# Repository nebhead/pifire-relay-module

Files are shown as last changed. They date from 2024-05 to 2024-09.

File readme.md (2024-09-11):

# PiFire Mechanical Relay Module PCB (v1.0.2) KiCad Files

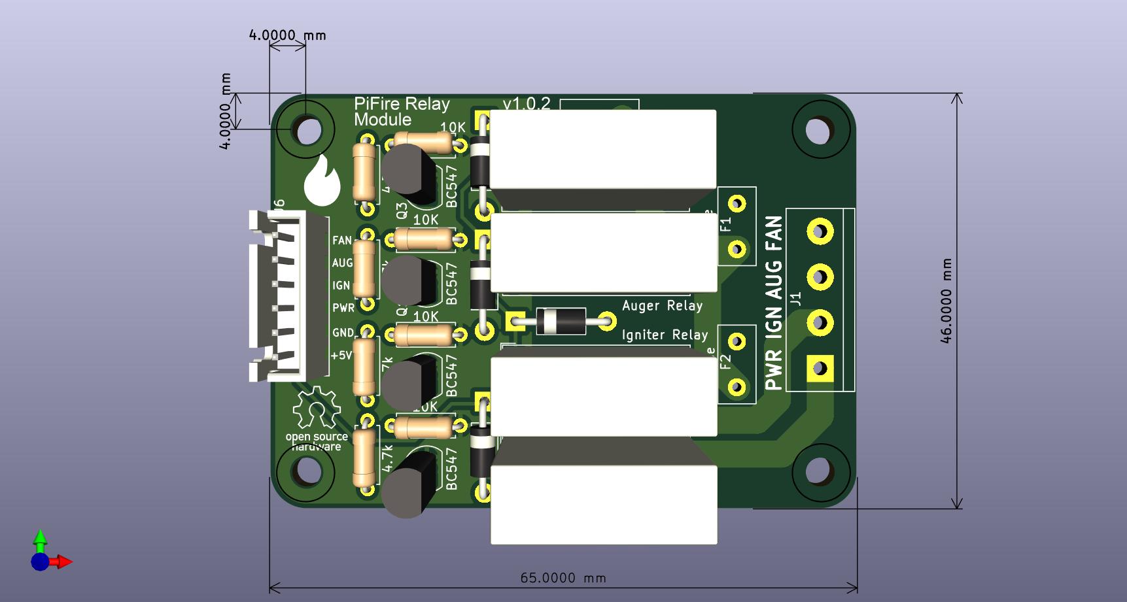
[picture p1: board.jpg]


## What is this? 

This PCB is designed to support mechanical relays for controlling incoming Power(L) to the Igniter, Auger, and AC Fan.  This board uses compact mechanical relays that are able to handle high power. This is an alternative to using an off the shelf relay module which simplifies the wiring and even allows you to use the OEM harness.  

The design intent for this board was to make a DIY accessible PCB that can be more easily put together by the maker/enthusiast of almost any skill level.  Full size components are used in most cases and most (if not all) parts should be readily available to order online.  See the [Interactive BOM](#interactive-bom) for more details about the parts used and links to order.

### What is PiFire? 

PiFire is a SBC based Pellet Smoker Controller.  More details can be found [here](https://nebhead.github.io/PiFire) or [at the GitHub repo](https://github.com/nebhead/pifire). 

## What's in this Repository?

### KiCad Project Files 
In this repository you will find the latest KiCad design files for the  PCB.  Simply load the project file (.kicad_pro) into the KiCad software and you should be able to edit as needed.  Or if you just want to get this board made, jump to the production section below.

### Interactive BOM

There is an interactive BOM located in the [/bom](bom/) folder which details the parts and provides some pin information as well.  Use this to gather the components you may need to build this board out and refer back to it for placement help.    

[BOM + Pin Info](https://nebhead.github.io/pifire-relay-module)

_This is a standalone HTML file that was autogenerated by the excellent plugin for KiCad. See the plugin here: [https://github.com/openscopeproject/InteractiveHtmlBom](https://github.com/openscopeproject/InteractiveHtmlBom)_

### PDF of the Schematic

Preview the schematic in PDF format here: [Schematic](schematic.pdf)

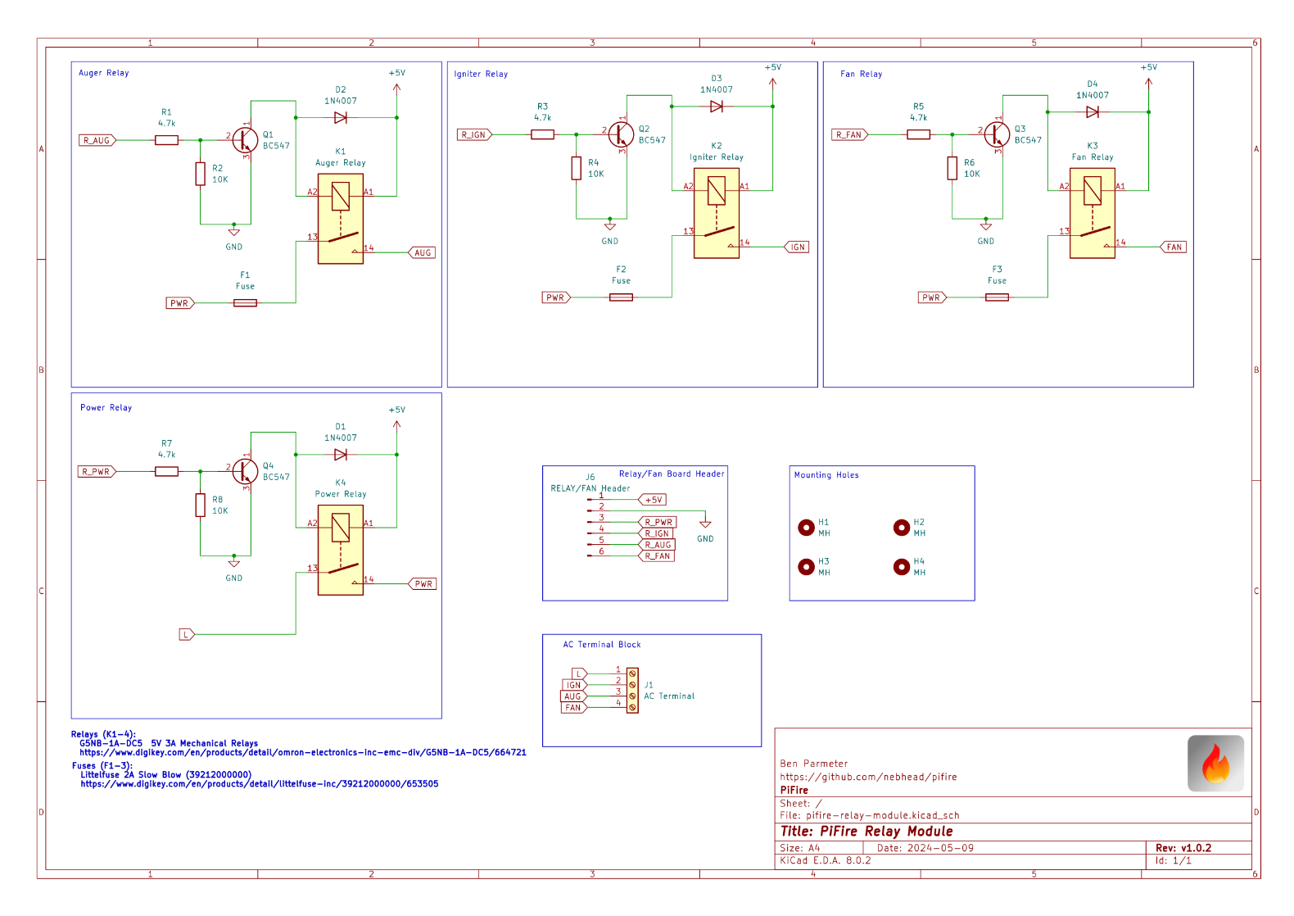
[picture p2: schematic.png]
Schematic PNG


### JLCPCB Production Files

If you wish to get these PCBs made by JLCPCB, the production files are provided in the `/production` folder.  For convenience, the file `production.zip` can simply be uploaded to JLCPCB to make it super easy to order boards.

Drop the zip file onto the order page, wait for it to upload then simply continue to order the board.  Optionally, select different board color, PCB quantity, surface finish, etc.  Most of the default settings should be sufficient. 

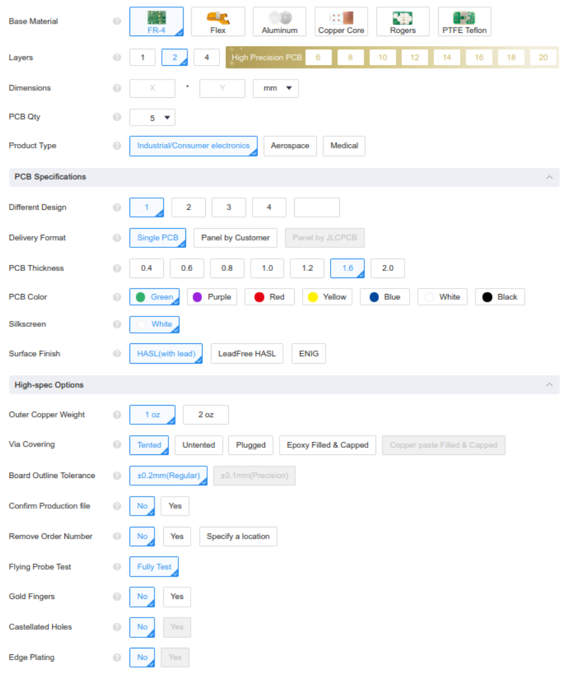
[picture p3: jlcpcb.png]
JLCPCB Order Page


### Links to the PCBs in this family of PiFire Boards

This PCB is part of a family of PCBs that can be used together to create  a full PiFire system.  Generally speaking you need the Main Module/Board, a Relay Control Board and a Probe Device board to have a basic PiFire system.  

**Main Module/Board** (required)
* [Main Board v4.0.x](https://github.com/nebhead/pifire-main-module-nopwr)

**Relay/Fan Control Boards** (choose one)
* [Mechanical Relay Module](https://github.com/nebhead/pifire-relay-module)
* [Solid State Relay Module](https://github.com/nebhead/pifire-relay-module-SSR)
* [Solid State Relay + PWM Fan Module](https://github.com/nebhead/pifire-relay-pwm-module-ssr) - Original Design
* [Solid State Relay + PWM Fan Module Alternate](https://github.com/nebhead/pifire-relay-pwm-module-ssr-alt) - Updated Design (Designed with help from @labmonkeyrat on Discord)

**Probe Device Board** (optional)
* [ADS Board](https://github.com/nebhead/pifire-ads-board) 

### 3D Printable Enclosures/Boxes 

With all of the 3D Prints for PiFire, a higher temperature filament such as PETG should be used.  PLA generally won't stand up to the temperatures that the components may be exposed to outdoors and near a hot smoker.  

#### Enclosure

Included here is an initial revision of the enclosure for this PCB.  The current models should be considered still in development and may have alignment challenges, etc. 

Except for the mounting wings, the majority of bolts to be used with this enclosure are M3. 

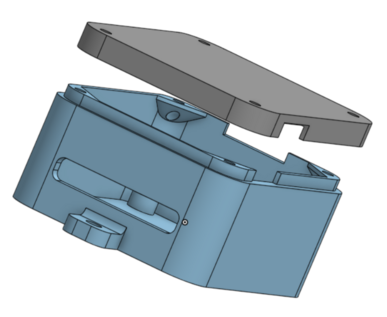
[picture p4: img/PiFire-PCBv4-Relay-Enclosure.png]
Enclosure


* STL: [Base](/printables/PiFire-v4-Relay-Base.stl)
* STL: [Lid](/printables/PiFire-v4-Relay-Lid.stl)
* OnShape: [Enclosure Original Models](https://cad.onshape.com/documents/03559f76f7adf190bf6f1259/w/7529cb0e4cd69db1a6a15202/e/07d5f9d46dc8f2b9e7dd655f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)

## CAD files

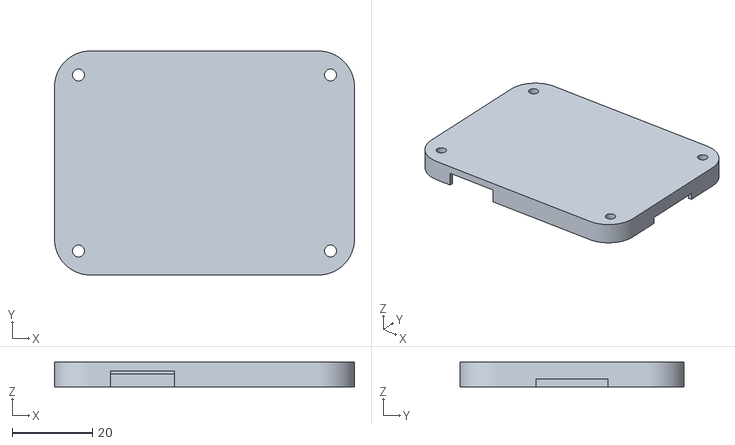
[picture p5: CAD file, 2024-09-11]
printables/PiFire-v4-Relay-Lid.stl
75.0 x 56.0 x 6.20

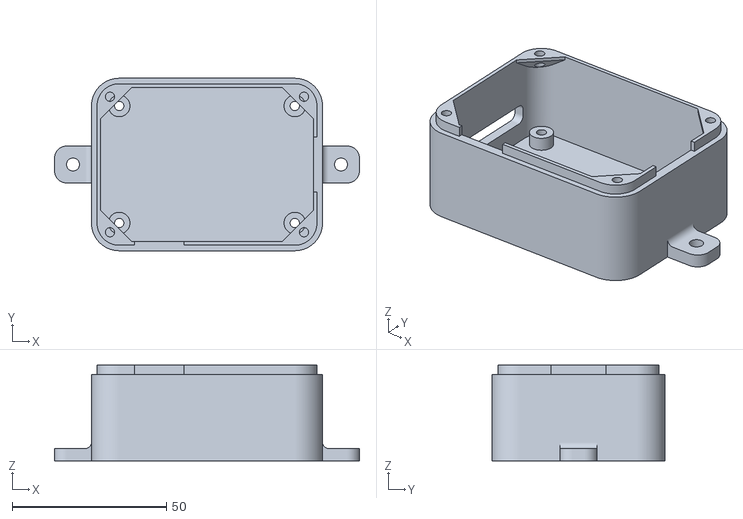
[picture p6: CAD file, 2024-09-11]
printables/PiFire-v4-Relay-Base.stl
99.0 x 56.0 x 31.0

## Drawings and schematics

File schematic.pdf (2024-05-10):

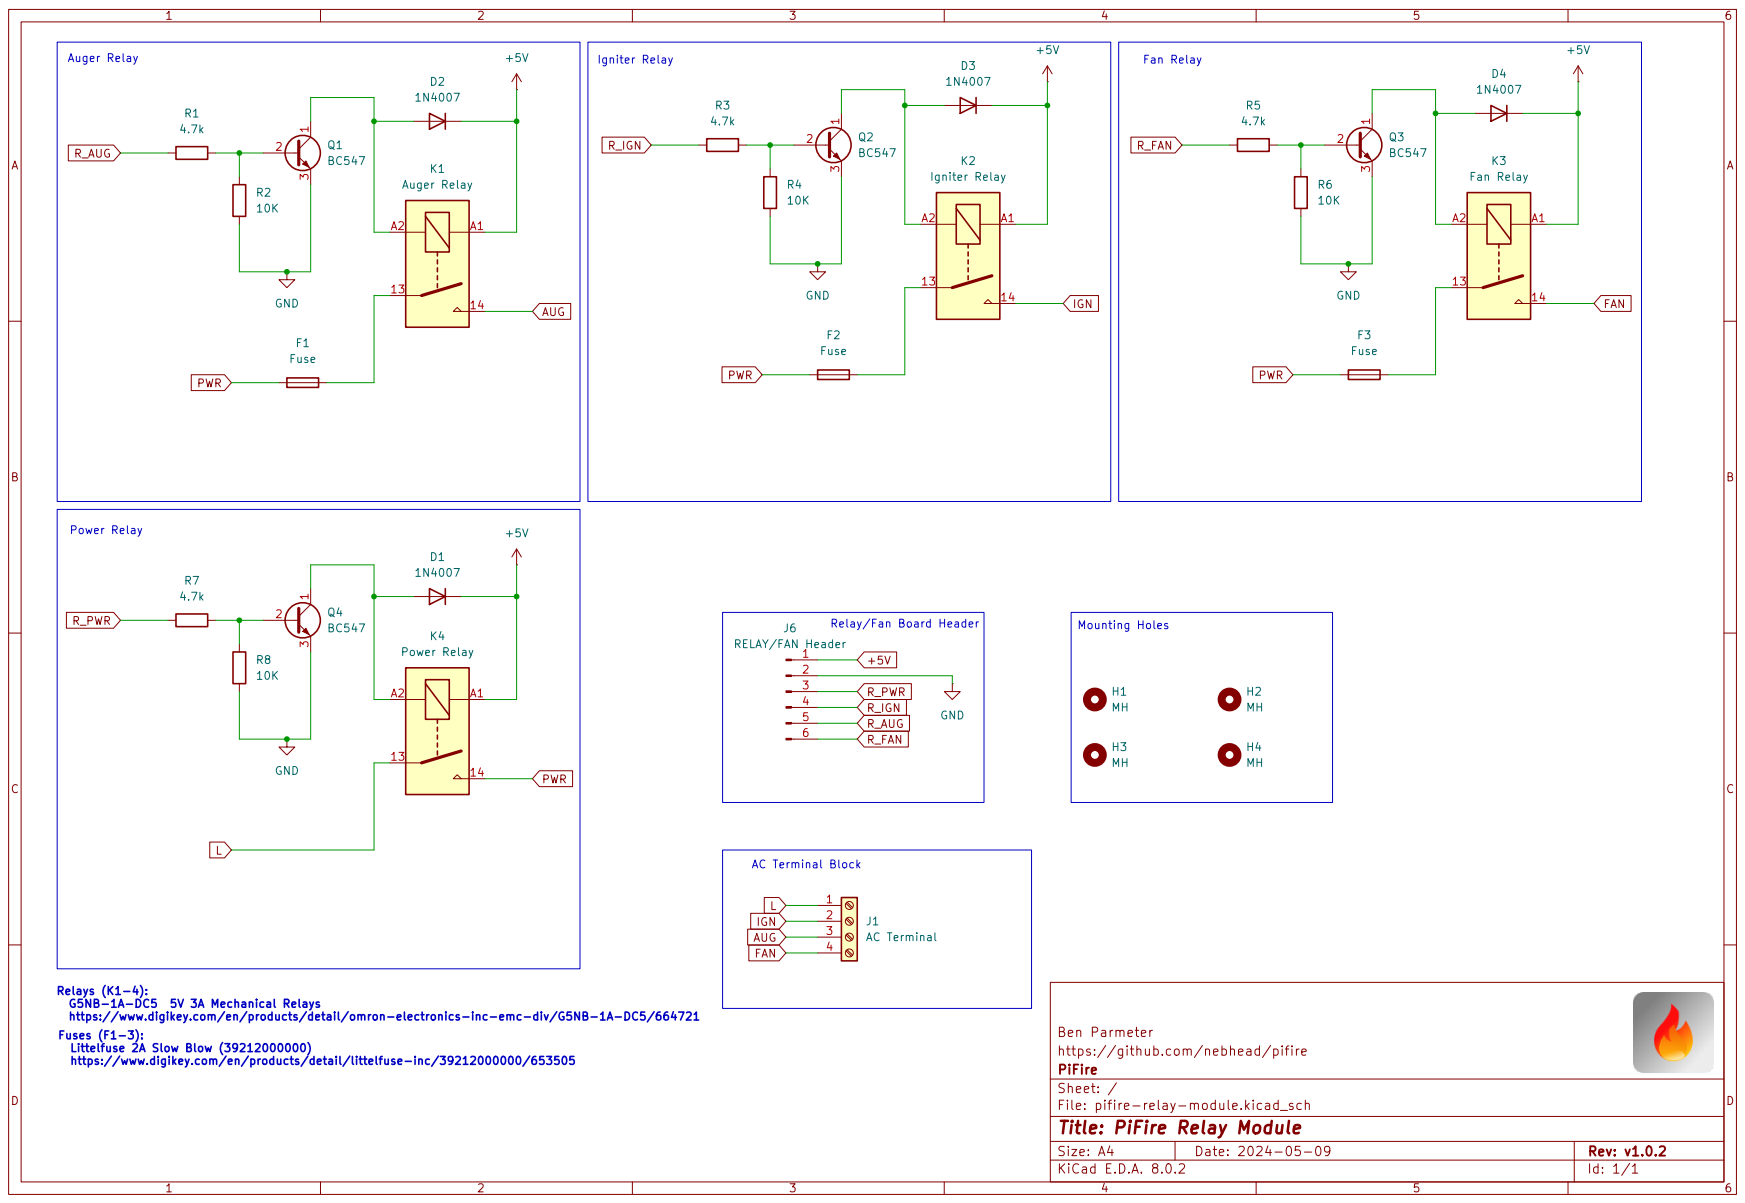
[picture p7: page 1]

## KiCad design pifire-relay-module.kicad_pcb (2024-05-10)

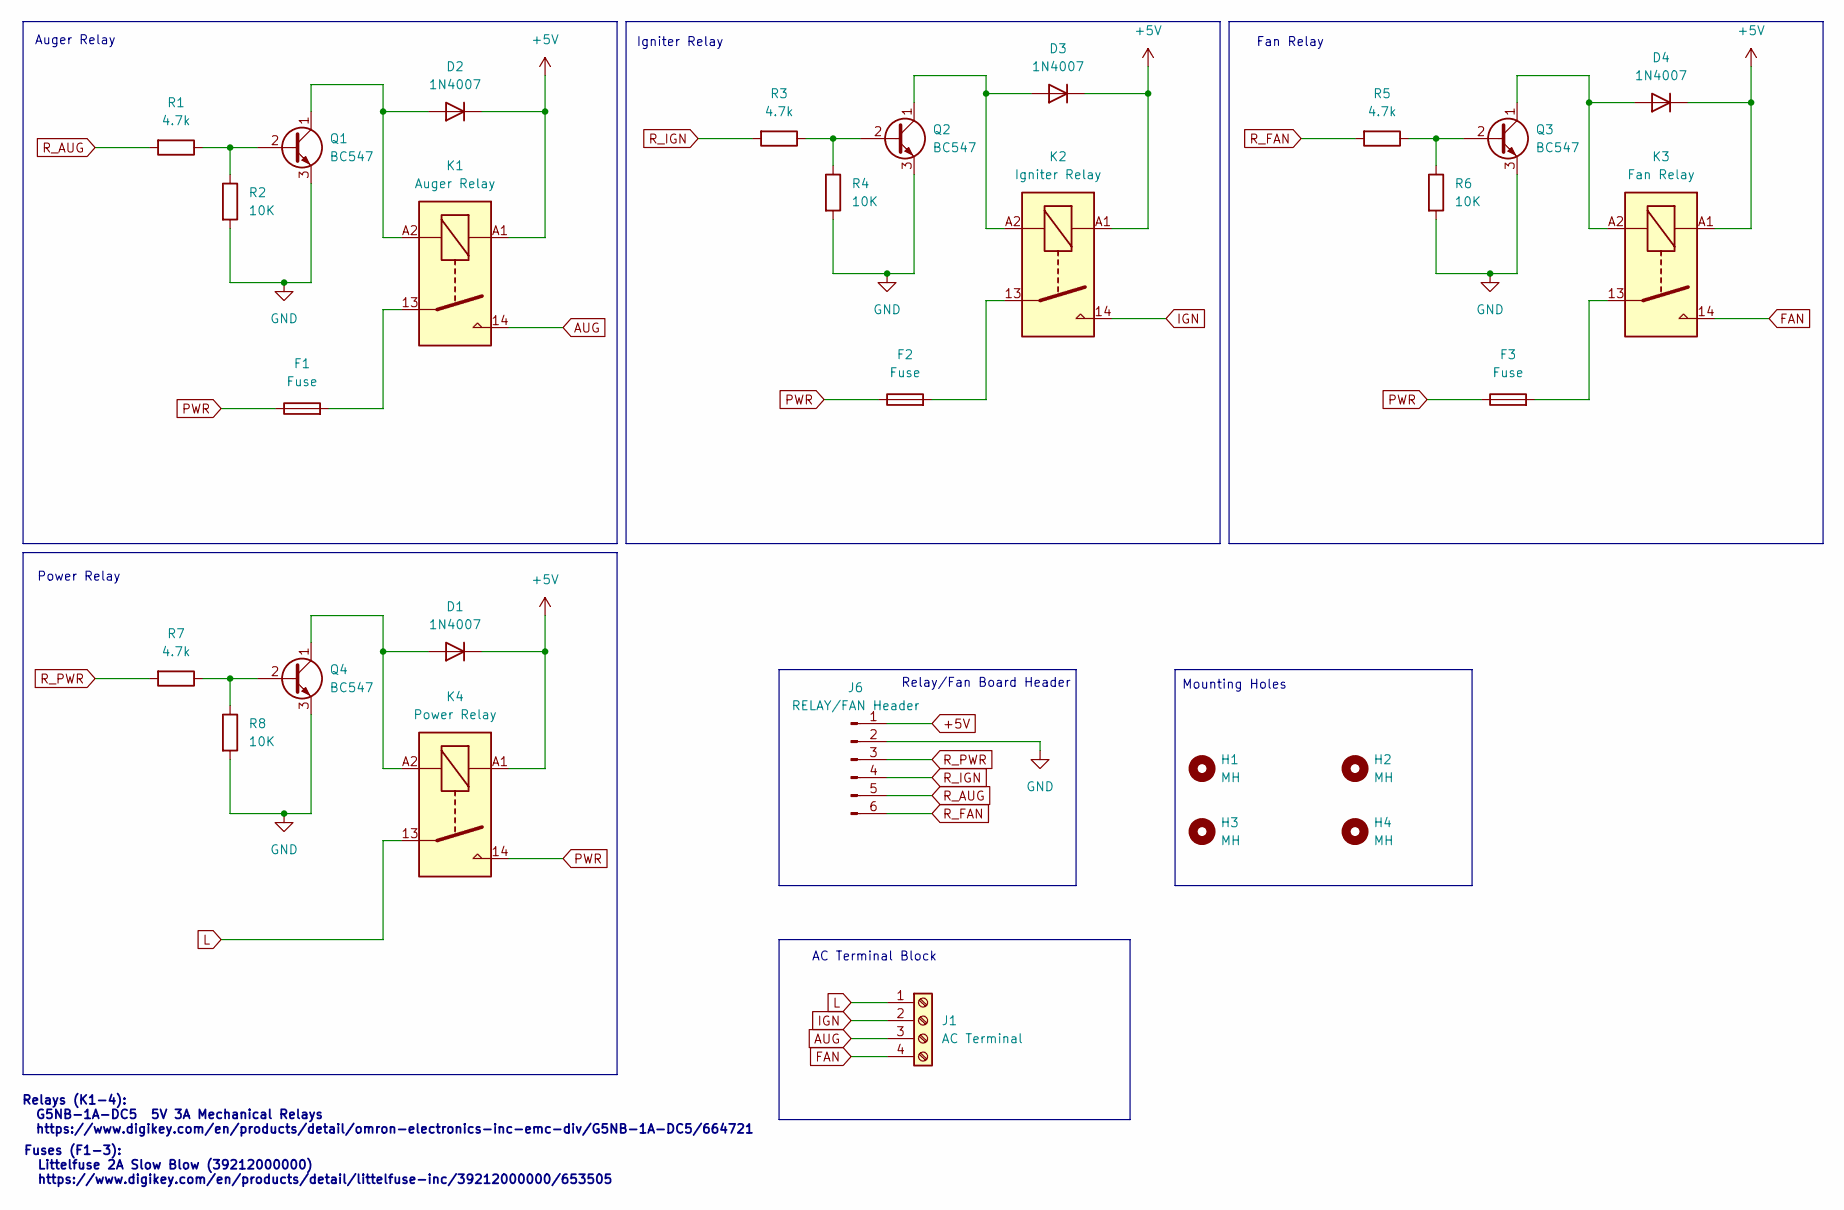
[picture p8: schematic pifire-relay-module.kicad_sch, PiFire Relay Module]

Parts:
D1, D2, D3, D4: 1N4007; D_DO-41_SOD81_P10.16mm_Horizontal
F1, F2, F3: Fuse; Fuse_Littelfuse_395Series
H1, H2, H3, H4: MH; MountingHole_3.2mm_M3
J1: AC Terminal; TerminalBlock_bornier-4_P5.08mm
J6: RELAY/FAN Header; JST_XH_B6B-XH-A_1x06_P2.50mm_Vertical
K1: Auger Relay; Relay_SPST_Omron_G5NB
K2: Igniter Relay; Relay_SPST_Omron_G5NB
K3: Fan Relay; Relay_SPST_Omron_G5NB
K4: Power Relay; Relay_SPST_Omron_G5NB
Q1, Q2, Q3, Q4: BC547; TO-92L_Inline
R1, R3, R5, R7: 4.7k; R_Axial_DIN0207_L6.3mm_D2.5mm_P7.62mm_Horizontal
R2, R4, R6, R8: 10K; R_Axial_DIN0207_L6.3mm_D2.5mm_P7.62mm_Horizontal

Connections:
+5V: D1.1 (K), D2.1 (K), D3.1 (K), D4.1 (K), J6.1, K1.A1, K2.A1, K3.A1, K4.A1
AUG: J1.3, K1.14
FAN: J1.4, K3.14
GND: J6.2, Q1.3 (E), Q2.3 (E), Q3.3 (E), Q4.3 (E), R2.2, R4.2, R6.2, R8.2
IGN: J1.2, K2.14
L: J1.1, K4.13
unnamed: D1.2 (A), K4.A2, Q4.1 (C)
unnamed: D2.2 (A), K1.A2, Q1.1 (C)
unnamed: D3.2 (A), K2.A2, Q2.1 (C)
unnamed: D4.2 (A), K3.A2, Q3.1 (C)
unnamed: F1.2, K1.13
unnamed: F2.2, K2.13
unnamed: F3.2, K3.13
unnamed: Q1.2 (B), R1.1, R2.1
unnamed: Q2.2 (B), R3.1, R4.1
unnamed: Q3.2 (B), R5.1, R6.1
unnamed: Q4.2 (B), R7.1, R8.1
PWR: F1.1, F2.1, F3.1, K4.14
R_AUG: J6.5, R1.2
R_FAN: J6.6, R5.2
R_IGN: J6.4, R3.2
R_PWR: J6.3, R7.2

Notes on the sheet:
Fan Relay
Power Relay
AC Terminal Block
Fuses (F1-3): Littelfuse 2A Slow Blow (39212000000) https://www.digikey.com/en/products/detail/littelfuse-inc/39212000000/653505
Auger Relay
Relay/Fan Board Header
Relays (K1-4): G5NB-1A-DC5 5V 3A Mechanical Relays https://www.digikey.com/en/products/detail/omron-electronics-inc-emc-div/G5NB-1A-DC5/664721
Mounting Holes
Igniter Relay

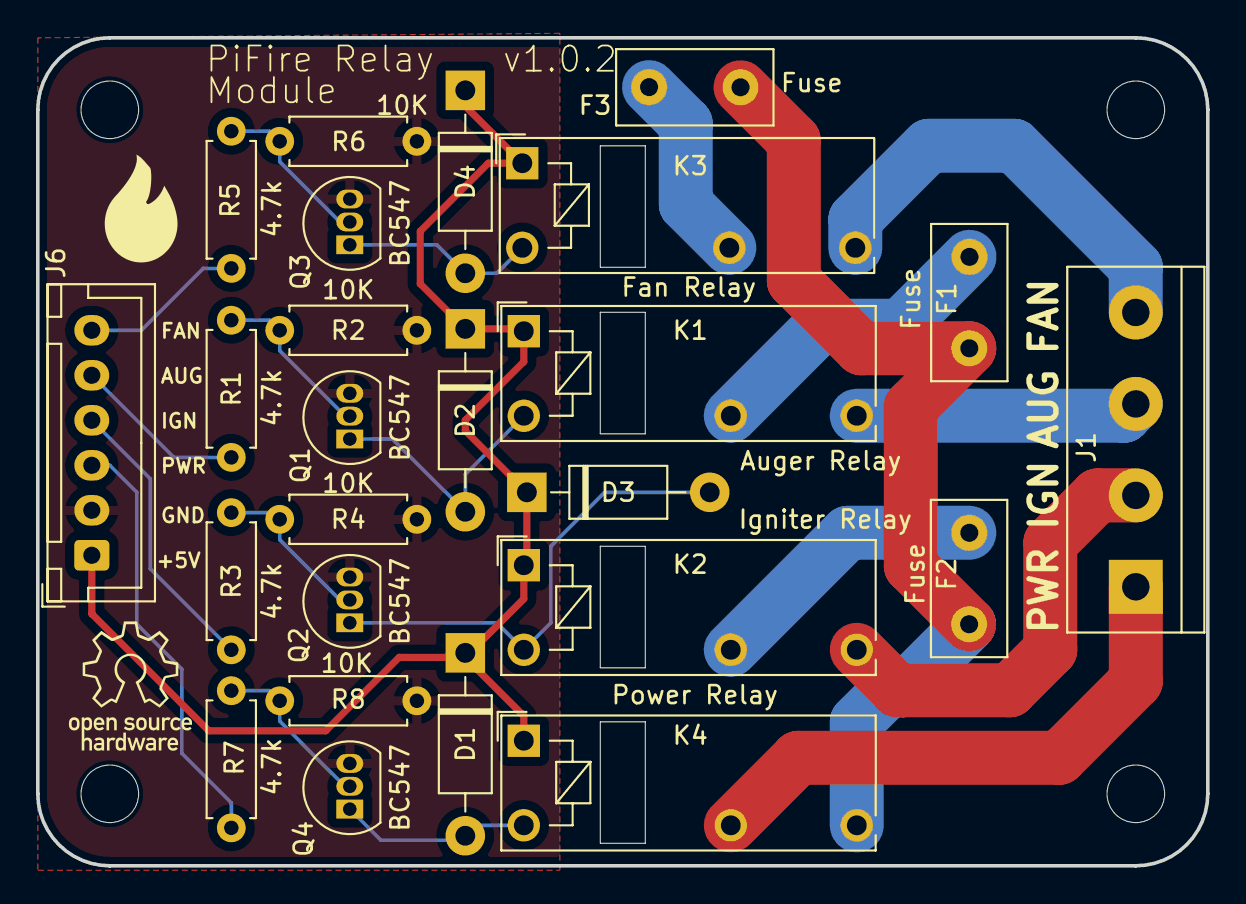
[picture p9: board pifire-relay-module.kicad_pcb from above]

Board: 2 copper layers, 65.0 x 46.0 mm, 29 parts (0 on the bottom side), 22 nets.

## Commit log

2024-09-07 Update readme.md
    Update links to the PWM boards.
2024-09-11 Auto stash before merge of "main" and "origin/main"
    [PiFire-v4-Relay-Base.stl, PiFire-v4-Relay-Lid.stl]
